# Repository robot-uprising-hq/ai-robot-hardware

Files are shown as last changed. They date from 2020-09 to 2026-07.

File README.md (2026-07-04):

# Micro Invaders - Hardware

This repository contains the hardware-related files of Robot Uprising Micro Invaders. The folder structure is as follows
* Root: Contains 3D printable basic robot parts
	* Accessories: Contains 3D printable accessories designed by Robot Uprising
	* Advanced: Contains design files
	* Images: Contains images mainly for README files
	* Misc: Contains miscellaneous 3D printable files related to the design, but not needed for the competition

The Micro Invaders robot is designed with simplicity in mind. It has very little amount of mechanical parts, and all the parts are 3D-printable. Moreover, it is designed to be assembled or disassembled without using any tools. 

If you need a 3D-printing guide, here is our guide: [3D-Printing Guide - Ultimaker 3](https://docs.google.com/document/d/1BAfrNYozn9PcpJIatZrwz-if5QTi_UQTAYi0SMTYilM/).

## Table of Contents <!-- omit in toc -->

- [Micro Invaders - Hardware](#micro-invaders---hardware)
	- [Mechanical parts](#mechanical-parts)
		- [Printing Checklist](#printing-checklist)
		- [Accesories](#accesories)
	- [Electronics](#electronics)
		- [Driver PCBA](#driver-pcba)
			- [PCB Gerber files and Bill of Materials](#pcb-gerber-files-and-bill-of-materials)
			- [PCBA Bill of Materials](#pcba-bill-of-materials)
		- [ESP32](#esp32)
		- [Motors](#motors)
		- [Batteries](#batteries)
		- [Cables and connectors](#cables-and-connectors)

## Mechanical parts

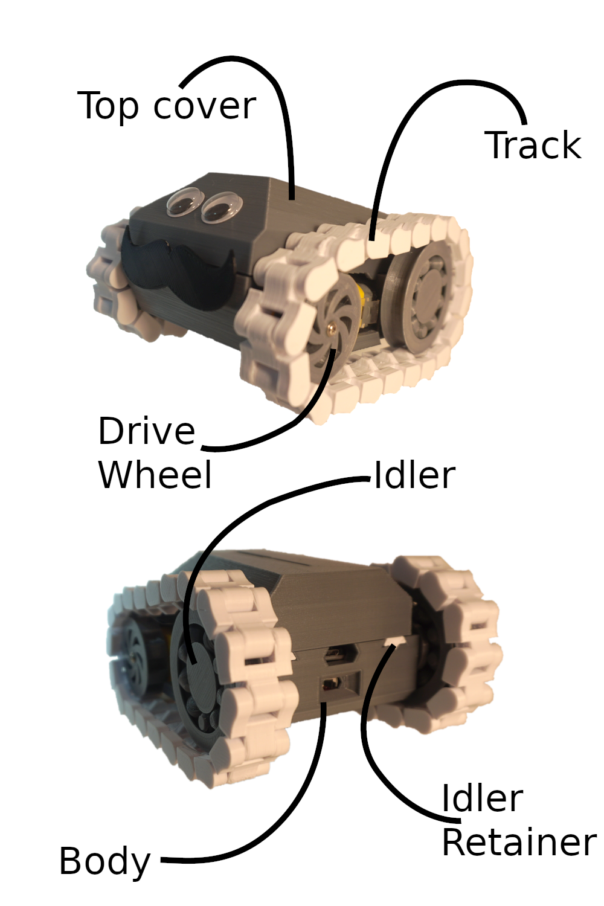
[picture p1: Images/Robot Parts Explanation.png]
Robot Parts Explanation


**Drive wheel:** This part drives the track, and the robot hence the name "drive wheel". The clearances are adjusted so that it fits nicely on the motor shaft, but it features a screw hole in case it doesn't.

**Idler:** This is the non-driving wheel for the tracks, but it also doubles as a tensioner. Thanks to its eccentric shaft, it can be used to adjust the slack on the chain.

**Idler retainer:** Idler retainer retains the idler :)

**Body:** This is the chassis of the robot. It houses all the parts. There are two versions of body. One is accessorizable and the other one is plain (located in Misc folder). As the name implies, accessorizable body is designed to fit accessories utilizing standard accessory connector.

**Top cover:** This part basically prevents things from falling off. It keeps the batteries in place, it prevents circuit board to fall off, and it even acts as the idler retainer retainer. All these functions in one single part. It attaches to the body by one rigid attachment point in the back, and one flexible attachment point in the front. This part also has two versions, accessorizable and plain (located in Misc folder).

**Track:** This is the part that moves the robot. It is basically a chain with 20 links.

### Printing Checklist

You will need to print the following parts for the competition.

| Amount | Part |
| :----: | --- |
| 1 | Body (accessorizable) |
| 1 | Top cover (accessorizable) |
| 1 | Aruco marker holder |
| 2 | Drive wheel |
| 2 | Idler retainer |
| 2 | Track |
| 2 | Idler |

See folders [Mechanics/Robot/STL](Mechanics/Robot/STL) and [Mechanics/Accessories/STL](Mechanics/Accessories/STL) for the STL-files for printing.

We recommend printing the parts in the given order as the latter parts are more advanced, and you might benefit from the experience. 
 
Also, feel free to design and print your own super exotic accessories or custom robot bodies for showing off between the matches, although you might not be allowed to use them in the competition. 

### Accesories

You can design and print your own front accessory as long as it complies with the [rules](https://github.com/robot-uprising-hq/ai-rules-mi2020).

## Electronics

### Driver PCBA

#### PCB Gerber files and Bill of Materials

You can find Gerber files for the PCB in the folder [Gerber Files](Electronics/Gerber%20Files). You can upload the compressed file to a PCB manufacturers website (e.g. JLCPCB)

Connect the right motor to J2 and the left motor to J3. Ensure motors have the correct polarity before fully assembling the robot to avoid unnecessary disassembly.

#### PCBA Bill of Materials

ID matches the schema and the PCB silkscreen

| ID | Description with link | Amount |
| :---: | --- | :----: |
| C1, C2 | [25V 100uF electrolytic THT capacitor](https://www.digikey.fi/en/products/detail/panasonic-electronic-components/ECA-1EM101B/268461) | 2 |
| D1, D2, D3, D4 | [RED clear 0805 SMD LED](https://www.digikey.fi/en/products/detail/liteon/LTST-C171KRKT/386801) | 4 |
| F1 | [2.5A (Max Hold Current), 5A (Trip Current) 16V Fuse 2920 (7351 metric) package](https://www.digikey.fi/en/products/detail/bel-fuse-inc/0ZCF0250FF2C/4156185) | 1 |
| J1 | [3-pin JST XH 2.50mm pitch connector](https://www.digikey.fi/en/products/detail/jst-sales-america-inc/S3B-XH-A/1651048) | 1 |
| J2, J3 | [2-pin JST PH 2.00mm pitch connector](https://www.digikey.fi/fi/products/detail/jst-sales-america-inc/S2B-PH-SM4-TB/926655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) | 2 |
| R1, R2, R3, R4, R6 | [1 kΩ 0805 SMD resistor](https://www.digikey.fi/en/products/detail/stackpole-electronics-inc/RMCF0805JT1K00/1757881) | 5 |
| R5 | [2.2 kΩ 0805 SMD resistor](https://www.digikey.fi/en/products/detail/stackpole-electronics-inc/RMCF0805JT2K20/1757894) | 1 |
| SW1 | [Slide switch](https://www.digikey.fi/en/products/detail/c-k/OS102011MA1QN1/1981430) | 1 |
| U1 | [7805 5V linear regulator (D2PAK Package)](https://www.digikey.fi/en/products/detail/onsemi/MC7805CD2TR4G/919332) | 1 |
| U2 (J4, J5) | [For ESP-32 two 20-pin 2.54mm pitch female headers which needs to be trimmed to 19 pins](https://www.digikey.fi/fi/products/detail/w%C3%BCrth-elektronik/61302011821/16608603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) | 2 |
| U3 | [Dual H-bridge motor driver 293D](https://www.digikey.fi/en/products/detail/stmicroelectronics/L293D/634700) | 1 |

### ESP32

ESP32-DEVKITC-32E:

- 1 x https://www.digikey.fi/en/products/detail/espressif-systems/ESP32-DEVKITC-32E/12091810

### Motors

Olimex LTD: MG-6-48

- 2 x https://www.digikey.fi/en/products/detail/olimex-ltd/MG-6-48/21662315

### Batteries

Two 18650 Li-Ion batteries (we recommend >2200mAh, with protection circuit):

- 2 x https://akkula.fi/tuote/xtar-18650-li-ion-akku-2600-mah-36v-suojapiiri-button-top/

Li-Ion 18650 battery charger:

- 1 x https://akkula.fi/tuote/xtar-mc2-plus-usb-pikalaturi-kahdelle-li-ion-akulle/

18650 battery holder for two batteries:

- 1 x https://akkula.fi/tuote/2-x-18650-asennuskotelo-johdoilla-max-1-a-virta/

### Cables and connectors

We recommend getting JST XH (2.50mm pitch) and PH (2.00mm pitch) connector assortment with crimp tool.
The JST connectors require crimping the cable ends with a tool such as https://www.partco.fi/fi/tyoekalut/puristuspihdit/loput-puristuspihdit/11353-ht213.html. 
Unless you're very much into crimping all the things, instead of buying the tool you can probably find one at your local university electronics lab, makerspace or https://hacklab.fi.

There are also preassembed wires: (we recommend 12" ones so that they are long enough)

XH:
https://www.digikey.fi/en/products/filter/jumper-wires-pre-crimped-leads/453?s=N4IgTCBcDaIFYGcAuACAHgCxAXQL5A

12" ones:
https://www.digikey.fi/en/products/detail/jst-sales-america-inc/ASXHSXH22K305/6684932

PH:
https://www.digikey.fi/en/products/filter/jumper-wires-pre-crimped-leads/453?s=N4IgTCBcDaIFYGcAuACADgCxAXQL5A

12" ones:
https://www.digikey.fi/en/products/detail/jst-sales-america-inc/ASPHSPH24K305/6009459

3-pin JST XH 2.50mm pitch Connector for battery terminal:
- Female 1 x https://www.digikey.fi/fi/products/detail/jst-sales-america-inc/XHP-2/555485

2-pin JST PH 2.00mm pitch Connector for motor terminals:
- Female 2 x https://www.digikey.fi/en/products/detail/jst-sales-america-inc/PHR-2/608607

### Firmware

There are two firmware repositories for this robot.
- Control the robot using a computer: [github.com/robot-uprising-hq/ai-robot-udp](https://github.com/robot-uprising-hq/ai-robot-udp)
	- Official firmware for receiving commands over WIFI (using UDP) and limited support for bluetooth
- Control the robot using a gamepad: [github.com/zero-ones-given/bluetooth-gamepad-robot-firmware](https://github.com/zero-ones-given/bluetooth-gamepad-robot-firmware)
	- Community built firmware for controlling the robot over bluetooth with a gamepad

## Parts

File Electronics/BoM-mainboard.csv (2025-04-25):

Reference | Value | Datasheet | Footprint | Qty | DNP
C1;C2 | 100uF |  | Capacitor_THT:CP_Radial_D6.3mm_P2.50mm | 2
D1;D2;D3;D4 | LED | ~ | LED_SMD:LED_0805_2012Metric | 4
F1 | b0250 2.5A | ~ | Fuse:Fuse_2920_7451Metric | 1
J1 | Conn_01x03 | https://www.tme.eu/en/details/s3b-xh-a-1/raster-signal-connectors-2-50mm/jst/s3b-xh-a-1-lf-sn/ | Connector_JST:JST_XH_S03B-XH-A_1x03_P2.50mm_Horizontal | 1
J2;J3 | Conn_01x02 | https://www.tme.eu/en/details/s2b-xh-a-1/raster-signal-connectors-2-50mm/jst/s2b-xh-a-1-lf-sn/ | Connector_JST:JST_PH_S2B-PH-SM4-TB_1x02-1MP_P2.00mm_Horizontal | 2
J4;J5 | Conn_01x19_Socket | ~ | Connector_PinSocket_2.54mm:PinSocket_1x19_P2.54mm_Vertical | 2
R1;R2;R3;R4;R6 | 1k | ~ | Resistor_SMD:R_0805_2012Metric | 5
R5 | 2.2k | ~ | Resistor_SMD:R_0805_2012Metric | 1
SW1 | Slide switch ON-ON |  | Button_Switch_THT:SW_CuK_OS102011MA1QN1_SPDT_Angled | 1
U1 | L7805 | http://www.st.com/content/ccc/resource/technical/document/datasheet/41/4f/b3/b0/12/d4/47/88/CD00000444.pdf/files/CD00000444.pdf/jcr:content/translations/en.CD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 | Package_TO_SOT_SMD:TO-263-2 | 1
U2 | ESP32-DEVKITC |  | mainboard:ESP32-DEVKITC | 1
U3 | L293 | http://www.ti.com/lit/ds/symlink/l293.pdf | Package_DIP:DIP-16_W8.89mm_SMDSocket_LongPads | 1

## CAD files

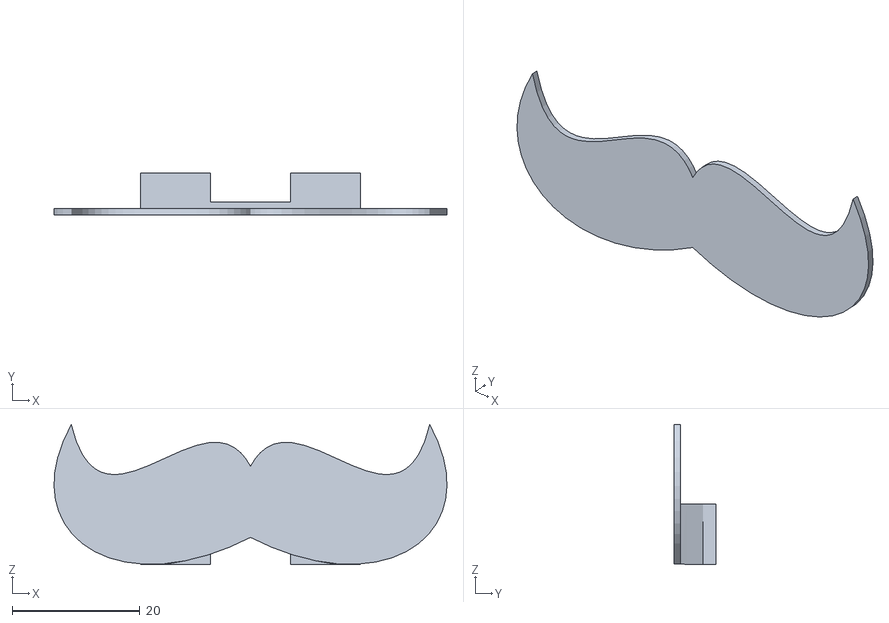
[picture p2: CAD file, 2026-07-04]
Mechanics/Accessories/STL/mustache_accessory.stl
61.5 x 6.50 x 21.9

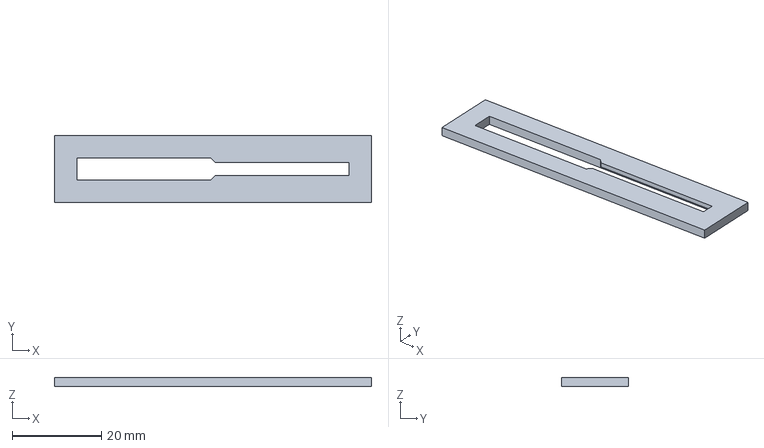
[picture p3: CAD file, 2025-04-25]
Mechanics/Accessories/top_accessory_template.fcstd
71.0 x 15.0 x 2.00 mm

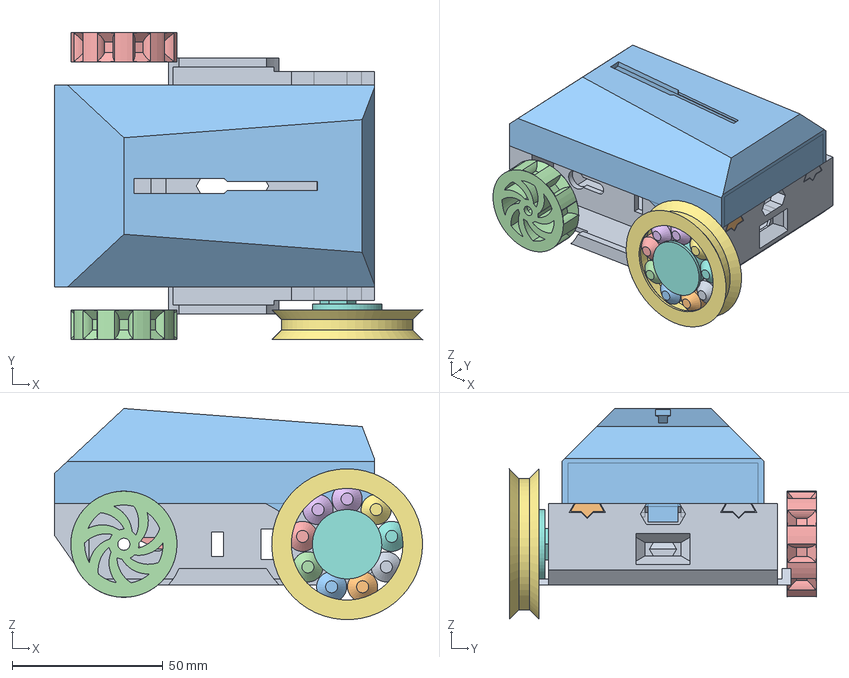
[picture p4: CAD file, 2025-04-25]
Mechanics/Robot/robot.fcstd
122.0 x 101.9 x 70.0 mm
lower_body
idler_retainer
upper_body
drive_wheel_left
drive_wheel_right
outer_race
inner_race
idler_retainer_right

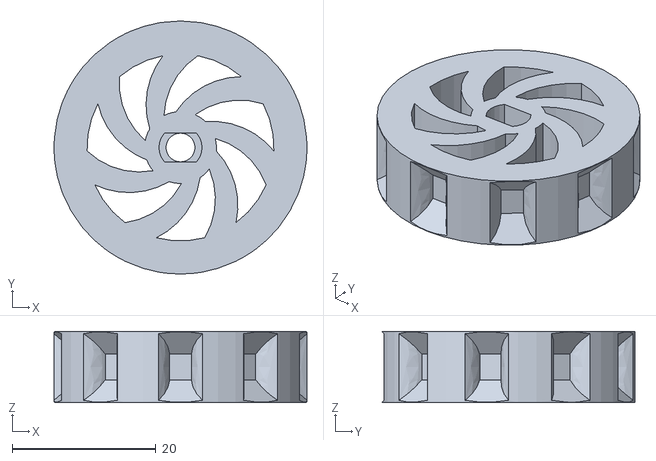
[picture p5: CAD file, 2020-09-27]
Mechanics/Robot/STL/driving_wheel.stl
35.2 x 35.2 x 9.90

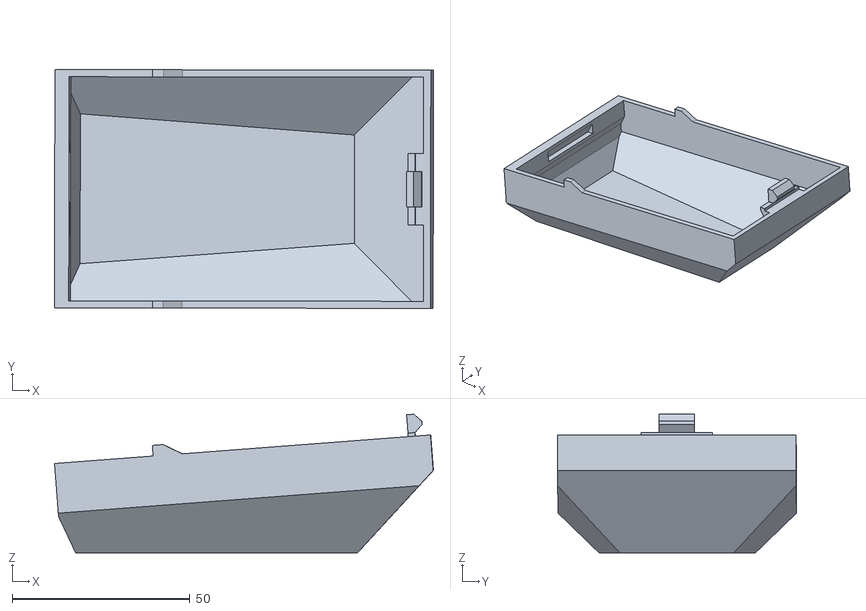
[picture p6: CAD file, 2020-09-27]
Misc/top_cover_plain.stl
106.6 x 67.2 x 39.0

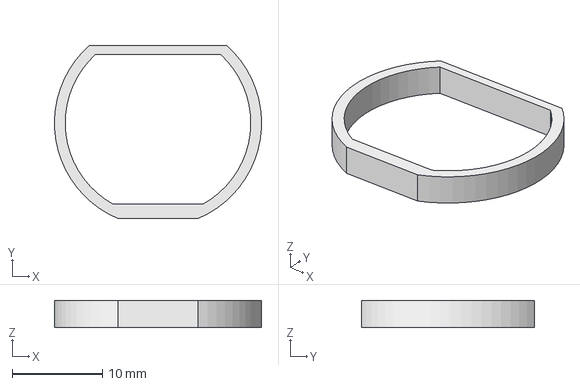
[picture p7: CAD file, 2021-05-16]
Mechanics/Accessories/motor_strain_relief.FCStd
23.0 x 19.2 x 3.00 mm

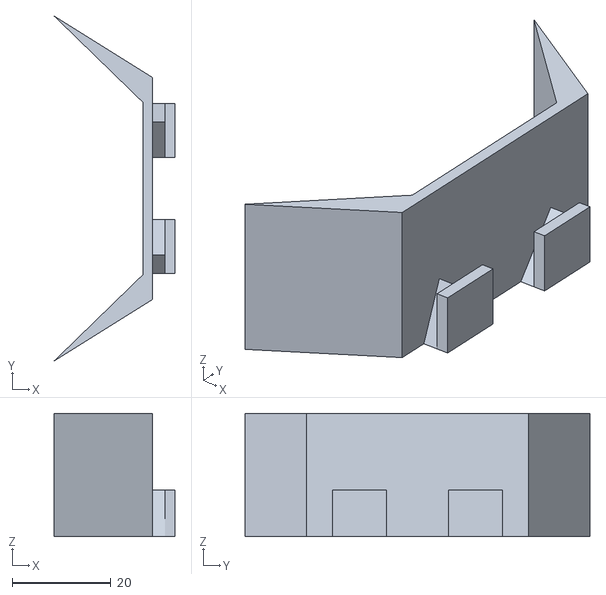
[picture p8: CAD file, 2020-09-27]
Mechanics/Accessories/STL/plower_small.stl
24.5 x 70.0 x 25.0

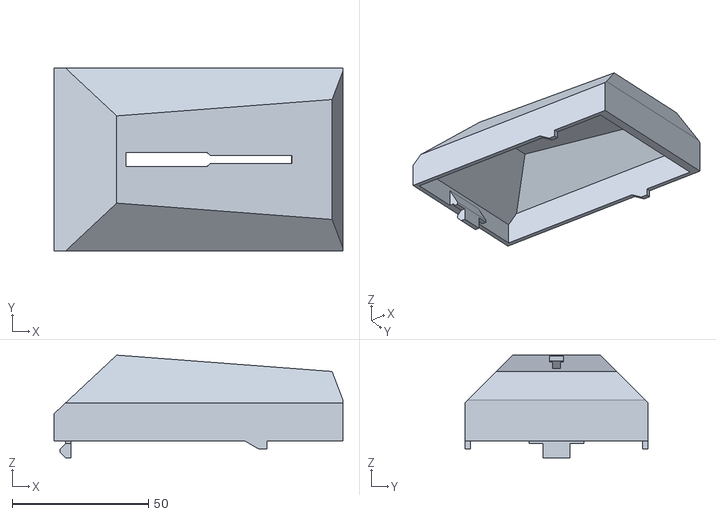
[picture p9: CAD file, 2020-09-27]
Mechanics/Robot/STL/top_cover_accessorizable.stl
106.0 x 67.0 x 37.7

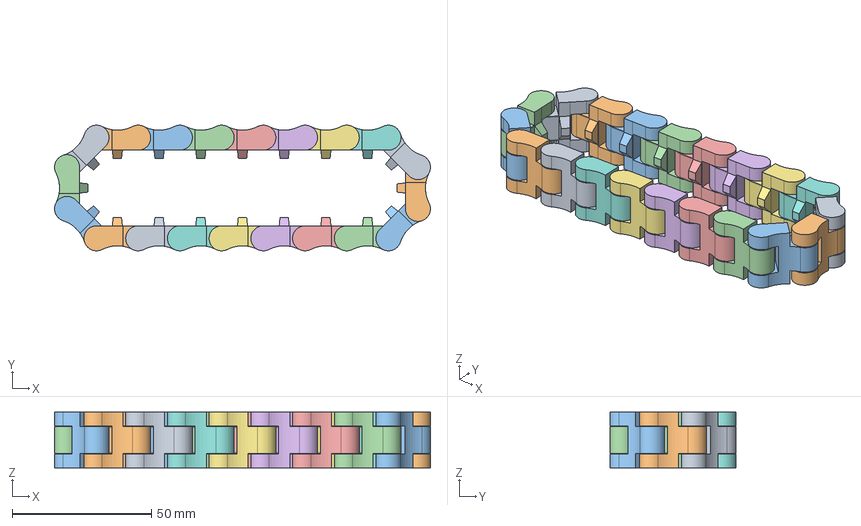
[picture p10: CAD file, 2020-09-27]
Mechanics/Robot/track.fcstd
135.2 x 45.2 x 20.0 mm

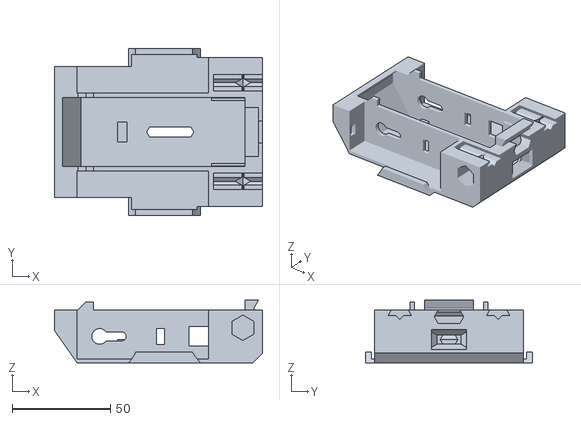
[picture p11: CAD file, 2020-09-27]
Misc/robot_body_plain.stl
106.0 x 85.0 x 32.0

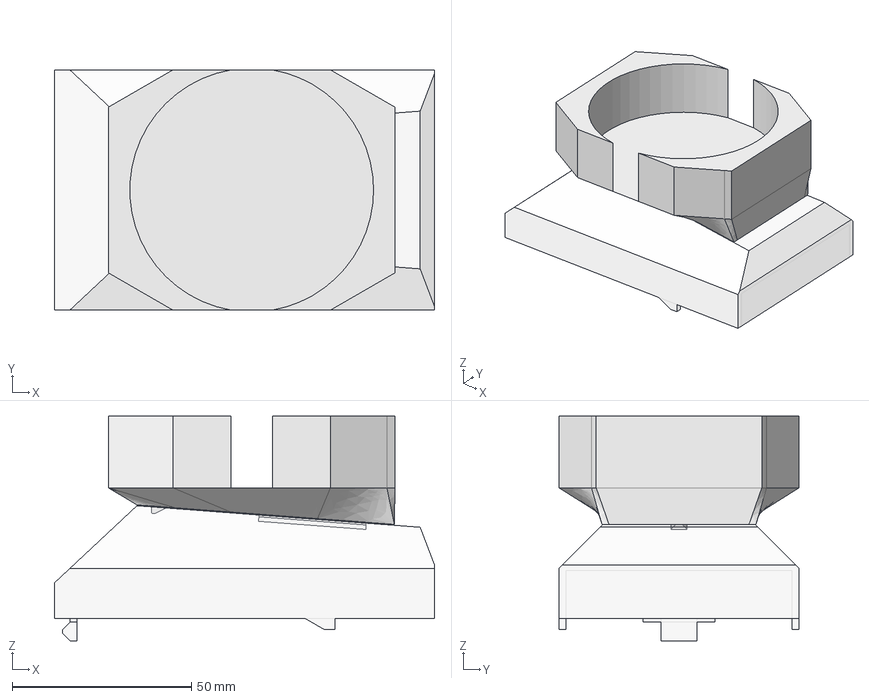
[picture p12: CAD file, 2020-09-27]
Mechanics/Accessories/beverage_holder.fcstd
106.0 x 67.0 x 62.7 mm
mounting
upper_body
marker_holder

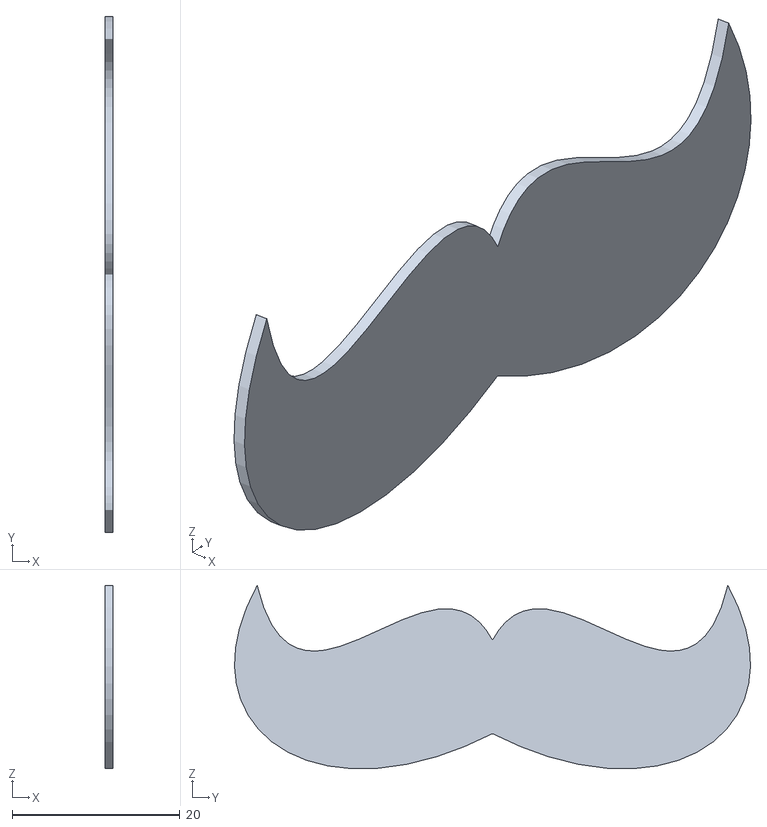
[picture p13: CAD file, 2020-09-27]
Mechanics/Accessories/STL/mustache_plain.stl
1.00 x 61.5 x 21.9

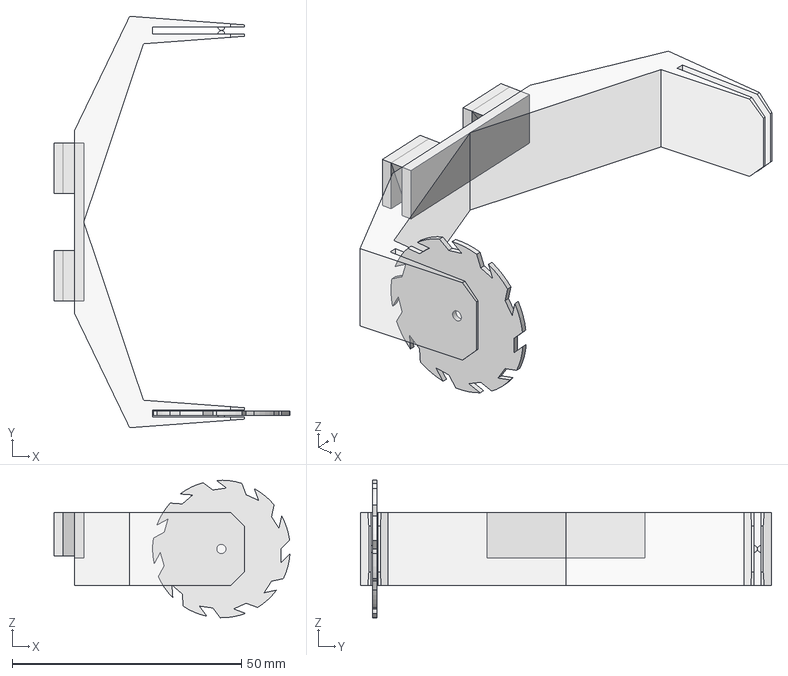
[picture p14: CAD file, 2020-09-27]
Mechanics/Accessories/front_accessory_template.fcstd
51.5 x 89.7 x 30.0 mm
template
plower2
plower2_blade

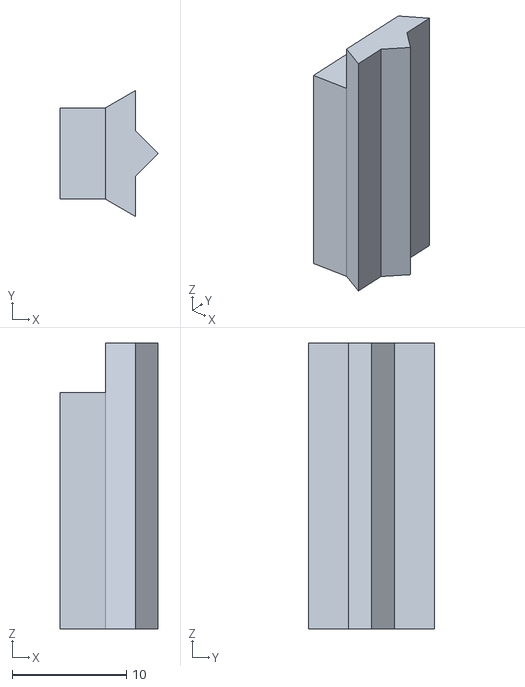
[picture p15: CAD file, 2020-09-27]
Mechanics/Robot/STL/idler_retainer.stl
8.60 x 11.0 x 25.0

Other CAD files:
Mechanics/Robot/STL/robot_body_accessorizable.stl
Mechanics/Accessories/aruco_holder.fcstd
Mechanics/Robot/STL/idler_ball.stl
Mechanics/Accessories/STL/aruco_holder.stl
Mechanics/Accessories/STL/front_accessory_template.stl
Mechanics/Accessories/STL/motor_strain_relief.stl
Mechanics/Accessories/STL/top_accessory_template.stl
Mechanics/Robot/STL/track.stl

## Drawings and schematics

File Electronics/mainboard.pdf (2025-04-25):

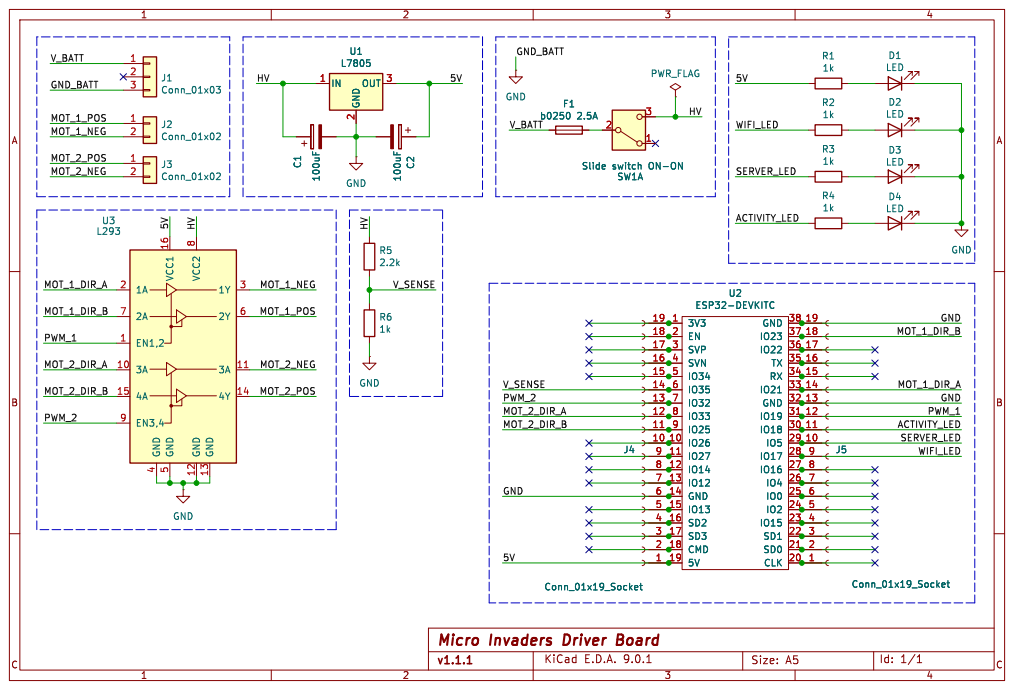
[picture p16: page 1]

Slide switch ON-ON

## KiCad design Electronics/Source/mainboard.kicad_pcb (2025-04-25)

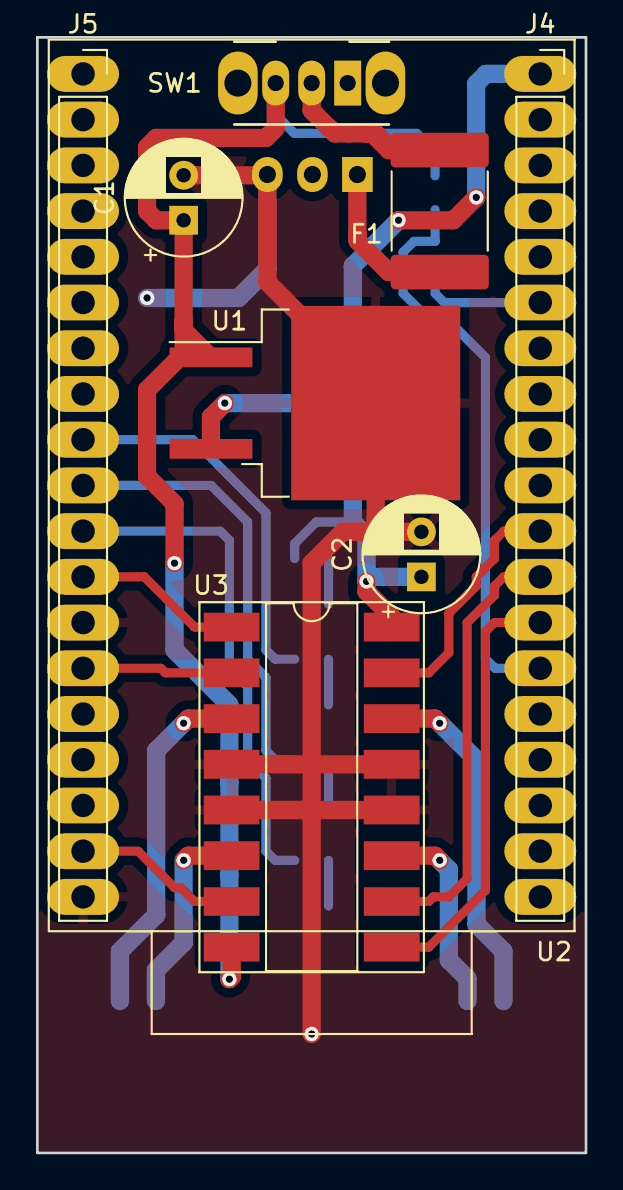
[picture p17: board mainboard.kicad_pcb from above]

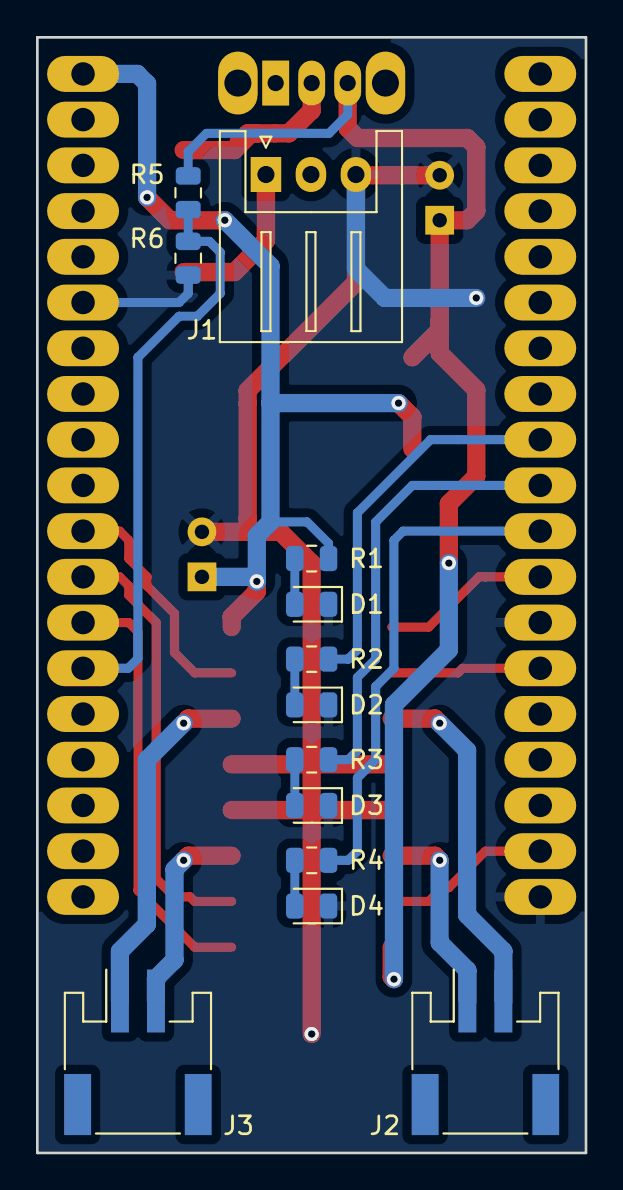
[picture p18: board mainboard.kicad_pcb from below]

Board: 2 copper layers, 30.5 x 62.0 mm, 22 parts (13 on the bottom side), 23 nets.

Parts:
C1, C2: 100uF; CP_Radial_D6.3mm_P2.50mm
D1, D2, D3, D4: LED; LED_0805_2012Metric
F1: b0250 2.5A; Fuse_2920_7451Metric
J1: Conn_01x03; JST_XH_S03B-XH-A_1x03_P2.50mm_Horizontal
J2, J3: Conn_01x02; JST_PH_S2B-PH-SM4-TB_1x02-1MP_P2.00mm_Horizontal
J4, J5: Conn_01x19_Socket; PinSocket_1x19_P2.54mm_Vertical
R1, R2, R3, R4: 330 ohm; R_0805_2012Metric
R5: 2.2k; R_0805_2012Metric
R6: 1k; R_0805_2012Metric
SW1: SW_DPDT_x2; SW_CuK_OS102011MA1QN1_SPDT_Angled
U1: L7805; TO-263-2
U2: ESP32-DEVKITC
U3: L293; DIP-16_W8.89mm_SMDSocket_LongPads

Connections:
/5V: C2.1, J4.1, R1.1, U1.3 (OUT), U2.19 (5V), U3.16 (VCC1)
/ACTIVITY_LED: J5.11, R4.2, U2.30 (IO18)
/GND: C1.2, C2.2, D1.1 (K), D2.1 (K), D3.1 (K), D4.1 (K), J1.3, J4.6, J5.13, J5.19, R6.2, U1.2 (GND), U2.14 (GND), U2.32 (GND), U2.38 (GND), U3.4 (GND), U3.5 (GND), U3.12 (GND), U3.13 (GND)
/HV: C1.1, R5.1, SW1.3 (C), U1.1 (IN), U3.8 (VCC2)
/MOT_1_DIR_A: J5.14, U2.33 (IO21), U3.2 (1A)
/MOT_1_DIR_B: J5.18, U2.37 (IO23), U3.7 (2A)
/MOT_1_NEG: J2.2, U3.3 (1Y)
/MOT_1_POS: J2.1, U3.6 (2Y)
/MOT_2_DIR_A: J4.12, U2.8 (IO33), U3.10 (3A)
/MOT_2_DIR_B: J4.11, U2.9 (IO25), U3.15 (4A)
/MOT_2_NEG: J3.2, U3.11 (3A)
/MOT_2_POS: J3.1, U3.14 (4Y)
/PWM_1: J5.12, U2.31 (IO19), U3.1 (EN1,2)
/PWM_2: J4.13, U2.7 (IO32), U3.9 (EN3,4)
/SERVER_LED: J5.10, R3.2, U2.29 (IO5)
/V_BATT: F1.2, J1.1
/V_SENSE: J4.14, R5.2, R6.1, U2.6 (IO35)
/WIFI_LED: J5.9, R2.2, U2.28 (IO17)
unnamed: D1.2 (A), R1.2
unnamed: D2.2 (A), R2.1
unnamed: D3.2 (A), R3.1
unnamed: D4.2 (A), R4.1
unnamed: F1.1, SW1.2 (B)

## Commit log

2020-09-27 Robot STLs added, some accessories added
    [aruco_holder.stl, driving_wheel.stl, freewheel_retainer.stl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]
2020-09-27 CAD files added for the robot & electronics
    [aruco_holder.fcstd, beverage_holder.fcstd, drive_wheel.fcstd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]
2020-09-29 Printing checklist added
2020-09-29 Minor printing order change
2020-09-29 Add a link to 3D-printing guide
    Also changes the order of some sentences.
2020-10-25 Bumps on the arena added
    [bump_1.stl, bump_2.stl, bump_3.stl]
2021-05-16 Motor cable strain relief added
    [motor_strain_relief.FCStd, motor_strain_relief.stl]
2024-04-15 Added Gerber files and BOM
2024-04-15 Edited cables and connector BOM
2024-04-15 updated KiCad project
2024-04-15 cleaned up v2 KiCAD project files
2025-04-25 v1.1.1
    Restructured folders
    [BoM-mainboard.csv, aruco_holder.fcstd, aruco_holder.stl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]
